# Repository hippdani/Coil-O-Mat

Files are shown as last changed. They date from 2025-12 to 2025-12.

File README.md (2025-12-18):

# Coil-O-Mat
Coil winding machine with integrated turn counter.

The main body of the coil winder is made primarly of 3D-printed parts and some of the shelf hardware.
The turn counter is based on a Rapberry Pi Pico reading two mechanical switches witch are actuated by a cam on the handle. A 2x16 character LCD screen is used to display the turn number and other information.

Spulenwickler v9

# PCB
The PCB can be ordered using the gerber and drill files. The neccessary files are bundled in a .zip for your convenience. This .zip can directly be used to order from manufacturers such as JLC PCB (tested) or PCB Way.
You can use the [bill of materials](empty link) or just look on the backside of the board to populate it. It is recommended to not only solder the LCD on with the pin header but also screw it down using washers of the appropriate thickness for your display and pin header. STL files for the washers are not included, but i guess anyone can do their own from cylinders in the slicer if they really need to.
# Assembly 
Following parts are needed additional to the 3D-printed ones:

| Pcs. | Component |
|---|---|
| 1 | M10 threaded rod |
| 2 | Bearings 6000-2RS |
| 3 | M10 Nut DIN 934 |
| 1 | M3x15 Bolt with Nut |
| 4 | Wood screws |
| 2 | Micro switch with roller |
| 2 | M5x20 Hex head screw DIN912 |
| 1 | M6x40 Hex head screw DIN912 |
| 4 | M2.5 x 10 to 20 screw |
| 1 | <=3mm pin (optional) |

The microswitches should have the dimensions 20x10x6mm with 2.5mm mounnting holes in a distance of ~9.5 mm and should look similar to [this one](https://www.neuhold-elektronik.at/micro-schalter/micro-schalter-5a-250v-mit-rollen-hebel).
An optional wood plate can be used as base for more sturdiness, the wood screws will be used to mount the Coil-O-Mat to that or a table. The PCB comes with mounting holes, your free to mount it where ever you want. I recommend screwing it down next to the coil winders base. Make sure the cables wont get tangled in the handle.

For assembly first print the .stl files from the [3Dprints folder](https://github.com/hippdani/Coil-O-Mat/tree/main/3Dprints). It is recommended to print those parts from PETG. The '[clicker](https://github.com/hippdani/Coil-O-Mat/blob/main/3Dprints/clicker_v9_low_poly.stl)' can not be printed from PLA, because the integrated spring will creep over time and the ratched will stop working in a matter of days. pETG worked best in the testing, ABS seems suitable as well.

Press the bearings into place, cut the threaded rod to the length you desire and feed it through the bearings. Fix it with a M10 nut on both sides. Do not apply excessive force when tightening those nuts, otherwise the threaded rod will not rotate freely. Mount the clicker with two M5 screws, mount the micro switches onto the clicker and solder on wires. These wires need to be connected to J1 for one switch and J2 for the other switch. Changing which switch is connected to which port changes the direction for counting up / counting down. 

There are two versions of the handle, [R](https://github.com/hippdani/Coil-O-Mat/blob/main/3Dprints/cam_R_V9.stl) and [L](https://github.com/hippdani/Coil-O-Mat/blob/main/3Dprints/cam_L_V9.stl). The ony differnce is the direction in which the ratchet allows movement, use whatever you prefer.
Assemble the handle using the M6x40 screw and screw it onto the threaded rod. make sure to push the micro-switch rollers and clicker out of the way while mounting the handle, so they can properly engage.
If your handle is not thight enough, you can fix it with the <= 3mm metal pin after drilling through the threaded rod in line with the hole in the handle. If the handle slips on the threaded rod, the turn counting will be wrong! I do not recommend glueing on the handle, because the clicker is hard to exchange with a mounted handle and could need maintenace after some time.

Mount the carrier on the non-handle side of the threaded rod in your desired location. Drill through the threaded rod (3 mm - 3.5 mm) in line with the carriers mounting hole and fix it in place using the M3 screw and nut. One side of the carrier has a fitting recess for the hex nut. Depending on the coil you plan to wind you can put different carrier extensions on the carrier, a square one and a cone (cone actually not) are supplied with the .stl files. The other side of the coil carrier extension is pushed onto the threaded rod after the coil carrier / bobbin you intend to wind onto. It is tightened against the coil by another M10 nut.

Happy winding!

# Software
The software is developed using the Arduino IDE with [Earl Philhower's Pi Pico Core](https://arduino-pico.readthedocs.io/en/latest/). You need to install this to compile the code provided in the [code folder](https://github.com/hippdani/Coil-O-Mat/tree/main/software).
Alternatively, you can put the [.uf2 file](https://github.com/hippdani/Coil-O-Mat/tree/main/software) onto the Pi Pico, just like pasting a file onto a flash drive. The .uf2 file contains the compiled code.

# UX
Rotations are counted in half turns, the counter does decrease when the handle is turned in reverse direction.
## RESET
This button resets all counters to 0
## +/-
On a short press, this button increases the turn count by one and logs the increase in the second row of the display.
Same goes for the long press, where one is subtracted from the turn count.
## EEPROM
The Coil-O-Mat saves the numbers on the display in virtual EEPROM (flash memory). They will reapear after a power cycle. The code is not safe against power loss that happens exactly during a counting (handle, + or -) event. The storage feature is intended to be used when work is continued later and the machine is powered down in a controlled way.

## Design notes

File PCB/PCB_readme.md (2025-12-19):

# PCB

The PCB gerber files will be uploaded after they are de-branded and silkscreen text is translated to english.

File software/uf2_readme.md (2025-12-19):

# Install the .uf2 file onto the pi pico:

Push and hold the BOOTSEL button while connecting the Pi pica via USB to your PC. It should appear as mass storage device. Drag the [.uf2 file](https://github.com/hippdani/Coil-O-Mat/blob/main/software/Spulenwickelmitzaehlautomat.ino.rpipico.uf2) onto the Pi Pico. It should automatically reboot. Your done!

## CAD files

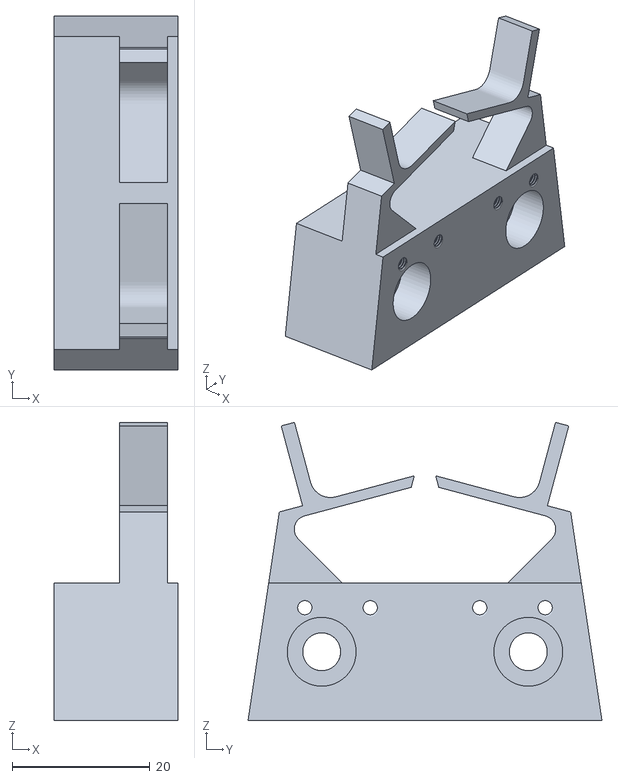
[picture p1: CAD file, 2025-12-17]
3Dprints/clicker_v9_low_poly.stl
18.0 x 51.4 x 43.3

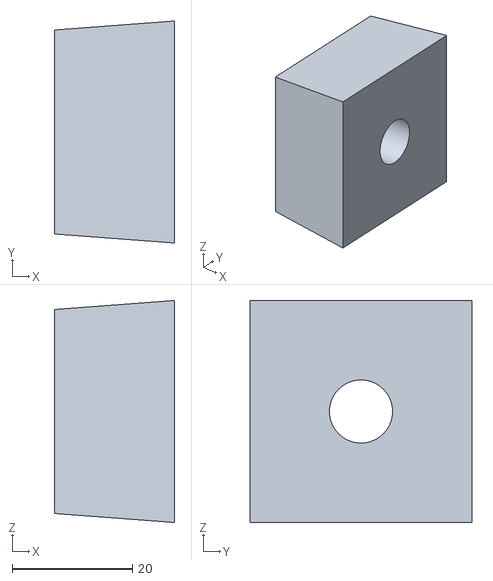
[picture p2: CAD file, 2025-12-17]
3Dprints/coilCarrierExtensionSquare.stl
20.0 x 37.0 x 37.0

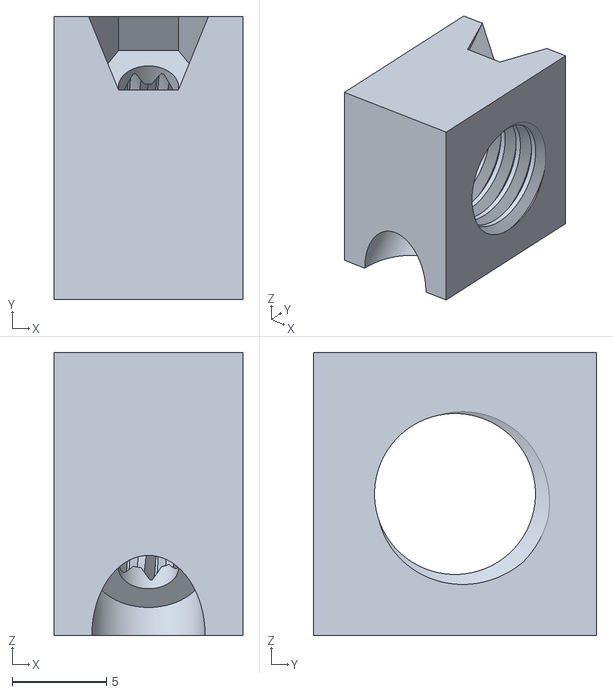
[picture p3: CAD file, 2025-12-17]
3Dprints/carrier_V5.stl
10.0 x 15.0 x 15.0

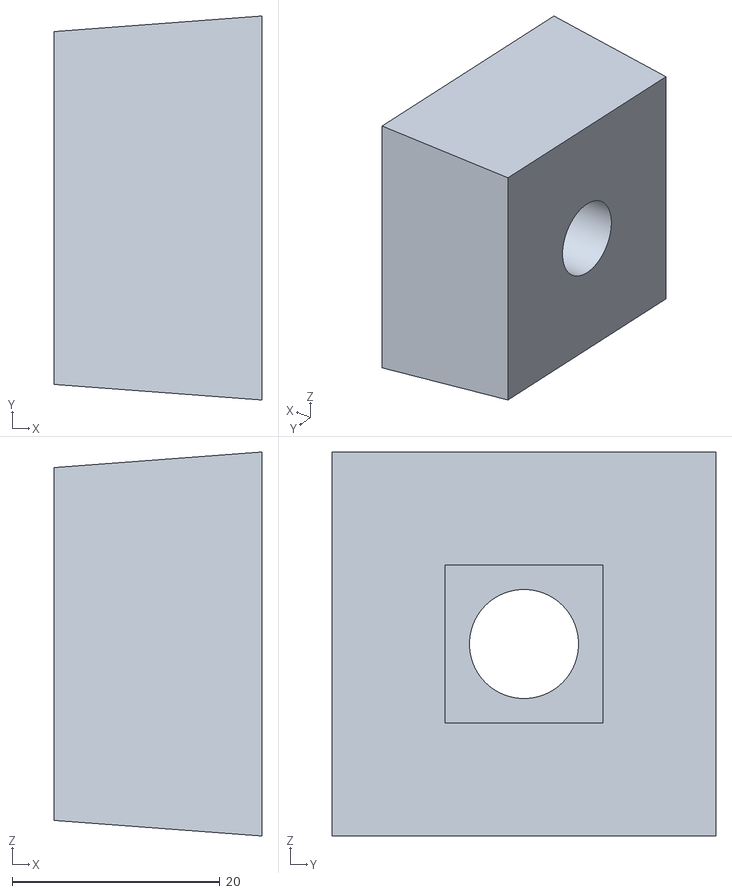
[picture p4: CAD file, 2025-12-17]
3Dprints/coilCarrierSquare.stl
20.0 x 37.0 x 37.0

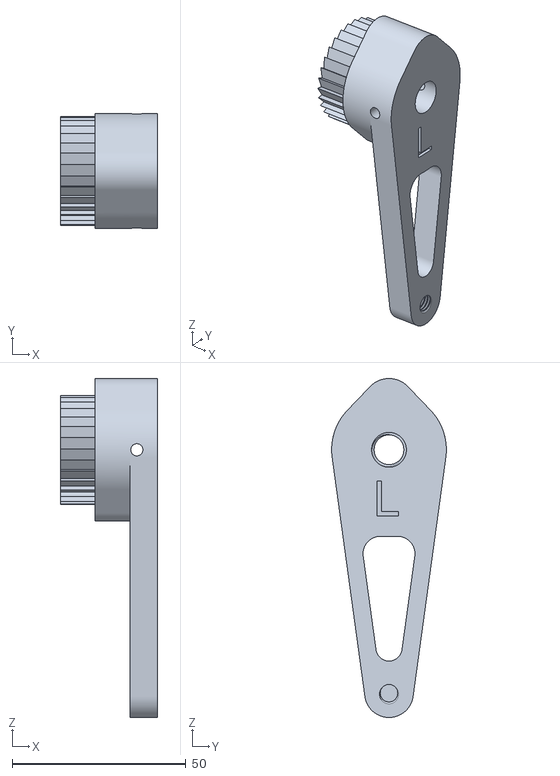
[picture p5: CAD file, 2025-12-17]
3Dprints/cam_L_V9.stl
28.0 x 33.0 x 97.5

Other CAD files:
3Dprints/cam_R_V9.stl

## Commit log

2025-12-17 Arduino files added via upload
2025-12-17 added stl files
    [cam_L_V9.stl, cam_R_V9.stl, carrier_V5.stl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]
2025-12-17 added clicker stl with lower polygon number to be < 25 MB
    [clicker_v9_low_poly.stl]
